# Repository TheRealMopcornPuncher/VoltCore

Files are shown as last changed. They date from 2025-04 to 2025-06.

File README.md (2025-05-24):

# VoltCore

A battery-powered variation of the common Cartesian 3d printer. Design specifications are subject to change.

Build volume: 100x100x65mm
Profile: Small
Battery: 24v 6ah lifepo4

VoltCore is a portable solution for 3D printing that allows an operator to print for one hour on a battery. This design attempts to solve the problem of environments devoid of immediate power via outlets or chargers connected to infrastructure.

- Amaya Allison & Jonathan Gallo

Image of printer

# Bill of Materials - VoltCore

| Item # | Description | Vendor | Part Number | Qty | Cost ($) | Purchase Link |
|---:|:---|:---|:---|---:|:---|:---|
| 1 | 2020 Aluminum Extrusions (200mm) | Amazon - VICHSAMWY | nan | 2 | $14.99 | https://www.amazon.com/European-Standard-Anodized-Aluminum-Extrusion/dp/B09JSNM85H/147-5007961-6940856 |
| 2 | Ender 3 Mainboard | Amazon - Creality Store | nan | 1 | $39.99 | https://www.amazon.com/Creality-Motherboard-Upgraded-Printer-TMC2225/dp/B0C77RBBP5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 |
| 4 | 24V 6Ah Lifepo4 Battery | Amazon - KBT | nan | 1 | $44.99 | https://www.amazon.com/letoom-LiFePO4-Rechargeable-Phosphate-Batteries/dp/B0DSRT3BB8 |
| 3 | E3D V6 Hot End Full Kit | Amazon - Ovenot | nan | 1 | $13.50 | https://www.amazon.com/Wangdd22-1-75mm-Printer-Extruder-Accessories/dp/B06XBXDJY3 |
| 4 | 1/8 inch PET Expandable Braided Sleeving | Amazon - Alex tech store | nan | 1 | $7.99 | https://www.amazon.com/25ft-Expandable-Braided-Sleeving-Sleeve/dp/B071G5L29C |
| 5 | T Nuts | Amazon - Socell | nan | 1 | $7.99 | https://www.amazon.com/Socell-180Pcs-Hammer-Fastener-Assortment/dp/B07Z4YH6NP |
| 6 | Belt Idler Pulley | Amazon - WINSINN | nan | 1 | $8.99 | https://www.amazon.com/WINSINN-Idler-Pulley-Timing-Aluminum/dp/B07BPHPYTN |
| 7 | Belt Timing Pulley | Amazon - Saipor | nan | 1 | $6.99 | https://www.amazon.com/Saiper-Aluminum-Synchronous-Compatible-Printer/dp/B07M9FT3H1 |
| 8 | Screws, Nuts, and Washers (Assortment/Kit) | Amazon - wugongshan | nan | 1 | $13.98 | https://www.amazon.com/Assortment-Machine-Washers-Phillips-Slotted/dp/B0BN297MP5 |
| 9 | Linear Rail (200mm) | Amazon - NUIBBYED | nan | 1 | $16.99 | https://www.amazon.com/MGN12H-Linear-Carriage-Printer-Machines/dp/B0BYVCXK88 |
| 10 | Voltage Regulator | Amazon - WWZMDiB | nan | 1 | $9.99 | https://www.pcbway.com/ |
| 11 | Flexible Shaft Coupler | Amazon - Eewolf | nan | 1 | $9.99 | https://www.amazon.com/Coupler-Flexible-Couplings-Printer-Eewolf/dp/B07BBP4H8C |
| 12 | Voron M4 Extruder Parts Kit | Amazon - FTVOGUE | nan | 1 | $15.60 | https://www.amazon.com/FTVOGUE-Accessories-Extrusion-Mechanism-Hardware/dp/B0BFCCTYDY |
| 13 | 5015 24v Blower Fan | Amazon - Richer-R | nan | 1 | $6.77 | https://www.amazon.com/Richer-R-Printer-Turbofan-Accessories-rotation/dp/B07CLG7RQY |
| 14 | 4020 24v Axial Fan | Aliexpress - YTF Technology | nan | 1 | $1.30 | https://www.aliexpress.us/item/3256803185681643.html |
| 15 | CR-Touch Leveling Probe | Amazon - Skouphy | nan | 1 | $39.00 | https://www.amazon.com/Creality-Leveling-Compatible-Mainboard-Printer/dp/B098LQ9WPX |
| 16 | NEMA 17 Stepper Motors | Stepperonline | 17HS13-0404S1 | 4 | $8.48 | https://www.omc-stepperonline.com/nema-17-bipolar-1-8deg-26ncm-36-8oz-in-0-4a-12v-42x42x34mm-4-wires-17hs13-0404s1 |
| 17 | Linear Ball Bearings | Amazon - Edoneery | nan | 1 | $11.99 | https://www.amazon.com/LM8UU-Linear-Bearings-Length-Printer/dp/B087WPGQ8T/147-5007961-6940856 |
| 18 | Linear Rods (200mm) | Amazon - akkacm | nan | 1 | $15.99 | https://www.amazon.com/Hardened-Chrome-Plated-Linear-Printer/dp/B09YRLS34X |
| 19 | (ONLY ONE OF EACH) 200mm Lead Screw and Lead Screw Nut | Amazon - VICHSAMWY | nan | 1 | $4.99 | https://www.amazon.com/400mm%EF%BC%8815-75-Inches%EF%BC%89Tr8x8-Thread-Printer-Machine/dp/B0BWYL5RNC |
| 20 | Split Shaft Collar | Amazon - PATIKIL | nan | 1 | $7.29 | https://www.amazon.com/PATIKIL-Thickness-Aluminum-Locking-Industry/dp/B0DDC83NVB |
| 21 | Needle Roller Thrust Bearings (2x) and Washers (2x) | Amazon - uxcell | nan | 1 | $6.19 | https://www.amazon.com/uxcell-Bearings-Diameter-Thickness-Hardness/dp/B07PDXYQTJ |
| 22 | GT2 Belt 6mm | Aliexpress - 	3DPrinterSuper Store | nan | 1 | $3.79 | https://www.aliexpress.us/item/3256808197552885.html |
| 23 | PEI Magnetic Buildplate (120mmx120mmm) | Amazon - G-hubble | nan | 1 | $10.99 | https://www.amazon.com/120x120mm-Textured-Magnetic-Adhesive-Printer/dp/B09TXM7VFC |
| 24 | Bowden Tubing | Amazon - Creality Store | nan | 1 | $5.99 | https://www.amazon.com/dp/B09WDGNZQM |
| 25 | Raspberry pi 0w | Amazon - Raspberry pi | nan | 1 | $22.78 | https://www.amazon.com/Raspberry-Pi-Zero-Wireless-model/dp/B06XFZC3BX |

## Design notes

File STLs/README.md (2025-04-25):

The following files are in this directory and are required for the final build:

TL;DR - Print 1 of every file except "ModF_Angle_Bracket.stl" (x10), "ModB_Belt_Clamp_Y" (2x), and "ModF_Plastic_Risers.stl" (4x)

/bed:
---
ModB_Bed_Mount.stl x 1
ModB_Belt_Clamp_Y x 2
ModB_Rail_Spacer.stl x 1
ModB_Underplate.stl x 1
---

/extruder
---
ModE_Extruder_Mounting_Bracket.stl x 1
---

/frame
---
ModF_Angle_Bracket_5.2mm.stl x 12 (alternative available)
Or
ModF_Angle_Bracket.stl x 12
ModF_Left_Linear_Tensioning_Bracket_A.stl x 1
ModF_Left_Linear_Tensioning_Bracket_B.stl x 1
ModF_Mainboard_Mounting_Bracket.stl x 1
ModF_Plastic_Spacer.stl x 4
ModF_Right_Linear_Tensioning_Bracket_A.stl x 1
ModF_Right_Linear_Tensioning_Bracket_B.stl x 1
ModF_Spool_Holder_Riser.stl x 1
ModF_Spool_Holder_Tube.stl x 1
ModF_Y_Axis_Stepper_Mount.stl x 1
ModF_Z_Axis_Stepper_Mount.stl x 1
---

/gantry
---
ModG_Left_Tensioning_Bracket_A.stl x 1
ModG_Left_Tensioning_Bracket_B.stl x 1
ModG_Right_Tensioning_Bracket_A.stl x 1
ModG_Right_Tensioning_Bracket_B.stl x 1
ModG_Sliding_Idler.stl x 1
ModG_Stepper_Spacer_&_Mounting_Plate.stl x 1
---

/printhead
---
ModP_Belt_Clamp_X x 1
ModP_CR_Touch_Mount.stl x 1
ModP_Hotend_Clamp_A.stl x 1
ModP_Hotend_Clamp_B.stl x 1
ModP_Printhead_Mounting_Bracket_A.stl x 1
ModP_Printhead_Mounting_Bracket_B.stl x 1
ModP_Radial_Cooling_Fan_Mount.stl x 1
---

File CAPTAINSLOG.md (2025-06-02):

Made by: @Amaya and @Jonathan G 
Repository link: https://github.com/TheRealMopcornPuncher/VoltCore
BOM: https://docs.google.com/spreadsheets/d/1q4xtd6th8_cM6Qn8iwp2R4_8qS0gYeFDji75B9E_PQI/edit?usp=sharing
Images: https://docs.google.com/document/d/1O2JPVw-2Jhm0MzPRCLd0zcRRRKDtKQYV07AwvWWCOpY/edit?usp=sharing

Fusion 360 PCB link: https://a360.co/4jejSvC (DEPRECATED - DOES NOT WORK)
Fusion 360 Printer assembly link: https://a360.co/3RkSeRq

Total hours so far: ~127 hours
- [x] I have a 3d printer or will be getting one before March 21st

---
NOTICE! Print files and quantity specifications listed in STLs folder on github repo. I'm printing all of the files in PLA with standard infill (lol) and 2mm layer height. Basic settings. Tolerances are baked into the models. 

This project has been resumed for the Highway event at Hackclub, per authorization of Dari aka Alex Ren

END OF NOTICE!

---
< Briefing >
A silly concept accidentally turned reality
Pitch: An extra portable and partially remote solution to printing without an active power source

---

# Day 0 - Preparations and planning

### Feb 4, 2025

I began by generating a timeline for me to operate within, as to avoid me procrastinating and not finishing the project at all.

**Deadline: Feb 11**

- Finalize battery system and power management.
    
- Generate a rough BOM (electronics, motors, extruder, frame materials, etc.).
    
- Confirm which parts I can salvage from my spare Sovol SV01 Pro.
    
- Research and select a control board + firmware (e.g., Klipper or Marlin).

**Deadline: March 31** _(Finalized Design & Parts Ordered)_

- Design a compact frame in CAD, ensuring it satisfies a small size profile (X and Y dimensions are 6-7 inches).
    
- Simulate motion system (belt routing, pulley positioning, etc.).
    
- Plan the mounting locations for electronics and battery.
    
- **Finalize the design and order all necessary parts.**

**Deadline: April 14** _(All Parts Arrived & Assembly Begins)_

- Assemble frame and install motors, belts, and pulleys.
    
- Wire up control board and power system.
    
- Perform first motion tests (homing, jogging, etc.).
    
- Mount and test the extruder and hotend (ensure >220°C capability).
    
- **All parts should be in by this date to stay on track.**

**Deadline: April 28**

- Flash firmware and configure motion system.
    
- Tune motion system and stepper settings.
    
- Ensure power consumption is within acceptable limits.
    
- Run first test prints and refine print quality.

**Deadline: May 4** _(Final Benchy Print Verified & Ready to Ship)_

- Complete final tuning and ensure prints are high quality.
    
- Verify folding mechanism and portability.
    
- Confirm battery efficiency for intended use.
    
- **Must have a successful Benchy print by this date!**

**Deadline: May 6** _(Ship Everything or Carry it with You)_

- Pack the printer securely for shipping.
    
- Ensure documentation and necessary tools are included.
    
- Consider taking it as a carry-on for guaranteed arrival.

Besides this, I've also done some research on suitable parts. Mostly minimal. Total time elapsed: 2 hours

# Day 1

### Feb 5, 2025

I felt pretty energized with the project today so I decided to start working on pushing my project into the tank with the others. (Started writing and journaling today, previous entry was made up for yesterday.) I intend to jot some stuff down into the BOM and continue fleshing out my solution for power. Mostly stuff from my first deadline/checkpoint.

I started my BOM by snatching and customizing a template for it off the web in google sheets. After creating the BOM, I started looking for the components I'd need to assemble the frame, and I got a recommendation for some of the nicest prices and highest class extrusions I could find from a company called 80/20 LLC.

After getting the link to the extrusion, I was going to start modeling it in Fusion 360, when I proceeded to fall down a rabbit hole of logo design. In the end, I installed Inkscape and began learning how to craft a nice looking logo to slap over the rest of this project.

I decided to take a break from learning how to use Inkscape. After hopping into a call with my brother and ranting about the project, he suggested I use a single motor for the Z-axis linked via a belt to support all sides of the bed (Maybe via linear rods/rails?)

Total time elapsed: 1 hr 40 mins

---

# Day 2

### Feb 6, 2025

Today was a little hectic so I'm mostly just pushing myself to keep going for the sake of progress. Maybe I'll get some coffee... besides the point though.

Attempts to fill out my bill of materials went pretty good today. I got a lot done in terms of meeting my Feb 11th deadline. The help of my brother, who's an experienced engineer, came in handy quite often since he knew more about this than I did, and told me whenever I added something that wouldn't work to the BOM, as well as giving me recommendations on where to look and what I could use.

I also am deciding to keep track of what 3d printed parts I'll need to model and make for this printer to function:

- Bed mounting bracket
    
- Extruder fan shroud and mounting bracket

Total time elapsed: 2 hrs 25 mins

---

# HIATUS PERIOD: Feb 6th - Feb 12th

### Project resumed.

I'll admit, I gave up. I didn't think I knew enough, I ran out of motivation, and there it just felt like this whole thing was a waste of time for someone inexperienced like me.

Then, I rejected that philosophy. Of course there was going to be hurdles, there always is. I just needed to get back up and keep working. Nothing I've ever done happened unless I told myself I could be capable, and I'm doing that right now.

---

# Day 3

### Feb 12th, 2025

Running partially behind schedule, I knew I needed to catch up, so I decided to use my time on this day to finish my B.O.M. and move on.

My biggest issue was the cost of the parts. In their current state, I was up to over 300 dollars, and not even completely done with the list. To cut down on cost, I began looking for cheaper alternatives to my existing parts.

I devised a plan regarding the frame: The bed would be 3d printed at a size contained inside of a 100mm by 100mm space and would be covered with masking tape. Frame will be joined with aluminum extrusions and metal brackets, then reinforced with 3d printed corner braces.

I ended up revising literally everything in my BOM and got the price down quite a bit. The next steps would be to figure out what I'm doing for my extruder and hotend, cooling fans, and my z axis.

Total time elapsed: 2 hrs

---

# Day 4

### Feb 17th, 2025

I ended up getting sick for a few days which kinda... super sucked, but I'm back and feeling moderately okay. I'm running low on time to meet my deadlines so it's time for me to reorganize and plan out what I'm doing next. Only really one of these needs a change.

**Deadline: Feb 20**

- Finalize battery system and power management.
    
- Generate a rough BOM (electronics, motors, extruder, frame materials, etc.).
    
- Confirm which parts I can salvage from my spare Sovol SV01 Pro.
    
- Research and select a control board + firmware (e.g., Klipper or Marlin).

I ended up finishing an entire disassembly in about an hour and a half.

Total time elapsed: 2 hrs

---

# Day 5

## March 30th, 2025

Panic time!!! The deadline is very very close and I don't entirely know if we'll be getting an extension. To combat this, I've invited one of my closest friends to help me with the project. It also helps that he knows significantly more than I do, and is an extremely fast worker. 

We've gotten the BOM pretty much completed, all that's left to do know is model and joint everything in Fusion 360 so we can see what we're missing and revise the BOM based on that data. Jonathan, my friend, ended up modeling a few things last night, which is why I'll be taking up modeling as much as possible for my current task of the day. 

I almost forgot to mention one of the more important changes we made to the project. We ended up having to change the motion system from corexy to cartesian. Ultimately, the decision was just made due to time constraints and the complexity of the corexy motion system, which we are simply not prepared for.

I intend to work all day.

Organization is key to this project, so I'm going to be modularizing and listing the parts of the printer I will need to model here:

Frame
	3x 100mm extrusions for the bottom
	2x 200mm extrusions for sides extending up
	1x 100mm extrusion for connecting 200mm extrusions at the top of the structure
	2x 200mm extrusions for the x-axis and the y-axis
Gantry (X-axis)
	Printhead: Extrusion and hotend assembly
	Stepper controlling movement
	200mm 2020 Extrusion
Buildplate/Bed
	Mounting solution to base of device
	200mm 2020 Extrusion
	(Mount higher in the structure to accommodate large battery)
Base
	Housing for electronics and IO/other interfaces
	3x 100mm 2020 Extrusions
Z-Axis or as I like to call it, "Elevator"
	Dual support from Z-axis lead screws, must allow gantry to travel up and down
	Stepper controlling movement
	2x 200mm 2020 Extrusions

Total time elapsed: 7 hrs

---

# Day 6

## March 31st, 2025

I made an immense amount of progress yesterday and I honestly feel like completing this project is very much possible. Although I had tasked my partner with creating a voltage regulator, I very stupidly forgot to specify what for... so I now need to create a voltage regulator. again. This time with the LM2576-5.0 voltage regulator, since *it* will work between the battery and the mainboard. Which, might I add, isn't much of an impressive battery TT

Since I'm very... uh... for lack of a better term uneducated, I'll be using Fusion 360 to design my PCB. Additionally, Fusion 360 and I seem to share that trait, so I'll need to give it some of the libraries myself, instead of being able to just find what I need in the software. Very fun stuff.

UPDATE: I let my partner know about the correct specifications and he agreed to revise it himself, yippie :D

I've also worked out our extruder situation considering the E3D V6 Hotend I picked earlier. This was important, because my stupid #$% didn't realize you... didn't have to design an extruder from scratch.... oh well.

We'll be using the Sherpa Mini.

All of this in mind... I'm fairly confident I can just- START with the final CAD model tomorrow :DD 
EXCITINGGGG

*I love you spring break <3*

Total time elapsed: 3 hrs

___

# Day 7

### April 1st

My computer exploded and I lost all of my project files.

Just kidding. :3

Today I've decided to model the full printhead. To do this, I'll need to create a holding mechanism or structure for the E3D V6 hotend that links up to the Sherpa Mini extruder. Shouldn't be too hard, but then, what do I know lol.

NOTES: Self supplying 2x motors with pre-fastened timing pulleys for the X and Y axis, self supplying 2x additional motors and flex couplings for Z axis (Will need to purchase lead screws). This leaves only one motor to be actually purchased for the extruder.

It's going to be tricky with clearance, but I just need to design an adapter between the E3D's obnoxious 16mm notch connector thingy and the even more obnoxious space consuming Voron M4 extruder (Which by the way we're using now instead of the Sherpa because it's so insanely inexpensive.)

Total time elapsed: 1 hour

---

# Day 8

### April 3rd

It's been an abysmal pain trying to use all of the models I've collected for this project for reasons beyond me. Despite that, I've continued to make progress, although extremely slowly. I've got no idea what I'm doing with this project and it's driving me insane.

Today, I hope to actually model the stupid gantry, but luck seems to despise me as of recent.

To make things different from my multiple prior attempts to design this, I'll be designing it in reverse, starting from the mount attached to the 2020 extrusion acting as a frame for the x-axis, and working my way up to the hotend.

Holy molay I forgot just how much music helps me to get out of depressive moods lol. I LOVE YOU RWBY SOUNDTRACK.

Also sidenote why do I write like... idk something fancy whenever I'm upset lol???

MODELING IS GOING GREAT I'VE DONE SO MUCH ON THE MOUNTING PLATE FOR THE PRINTHEAD YIPPIEEEEEE!!!

Update: Spent 3 hours modeling something I didn't need :D I LOVE LIFE GUYS I LOVE MY LIFEEEEEE!!!11111

(Also personal note: Pester my elder engineers more)

I know what I'm doing now. Just added a full kit of the ender 3's POM wheels and spacers to the BOM, so I'll just need to model or scrape those from somewhere to get them in Fusion 360 :P

GODSPEED TO YOU FUTURE ME

Total time elapsed: 4 hrs

---

# Day 9

### April 4th

New day, new stuff. I'm fetching the models for the "Isolation Column" and 5mm eccentric spacers I need to the POM mounted motion systems

Updating most of the spacers/washers, lock nuts, and other components in my final printhead/gantry assembly to fit with an M5 screw since I previously modelled them to interface with M4 screws.

After about 2 hours I finished redesigning the mounting plate for the printhead. Later today after a break, I'll model the notches for the ends of the belt and the mounting system for the extruder.

I forgot to log most of what I was doing so I'll speed run explaining all of it really really quickly. OKAY SO. I imported the aluminum extrusion (2020 x 200mm) and modeled everything around it, since HEY y'know, kinda a STUPID amount easier when you're modeling stuff in decending order of importance.

So anyways, I started with the extrusion, slopped in the POM Wheels and jointed them to the rail in Fusion 360, gave it a sliding joint because why the flip not (I spent way too much time doing that in school to not use it here), then I made a plate using the projected positions of the wheels hugging the extrusion. This was helpful because it allowed me to get a really good estimation of where the holes in the plate would need to be.

Then I had to research how to fasten the wheels to the plate and tighten them on the aluminum extrusion. To do this I simply stared at an image of the ender 3 and drank an abnormal amount of coffee before getting extremely jittery and crying over stupid stuff for like 2 hours. After this mindbogglingly stupid way of research, I learned what I was doing wrong. Eccentric nuts need a slot in the mounting plate to rotate in, otherwise they're useless.

Oh also yes I literally just stole I mean stole I mean stole I mean- borrowed the x-axis/gantry design of an ender 3. I LEARNED SOMETHING REGARDLESS, SO I DON'T WANNA HEAR IT, SHUSH.

BUT ANYWAYS, after figuring out what spacers to use, how the eccentric nut worked, where I could buy everything, etc. I got to work again. I put those holes into the mounting plate and then jointed everything together, spacers and all. That made me really happy and I thought I was done, but then I was like "wait no there's literally nothing on that plate", and so you'll never guess what I decided to do next. Actually I slept for like 10 hours, but AFTER THAT, I modeled.. heh.. you guessed it, a TRIANGLE SHAPED HOLE! ....It helped remove unnecessary material okay?

After wasting wayyyy too much time on that, I moved on to modeling the slots/notches for the belt, that was simple enough (HAHA NO JK IT TOOK HOURS AND AT LEAST 5 SEPERATE REDESIGNS. ALSO I CRIED AGAIN). After the notches were modelled I decided to move onto making a mount for the extruder, which took the most time by a LONG SHOT. I kept projecting sketches, revolving circular depressions, and otherwise just fumbling around with it until it looked semi-functionable. Then I fumbled with it some more and got this kind of like, pressure mount? You have to screw a plate that compresses the E3D V6 hotend into a groove that keeps it tightly secured. HOPEFULLY, THAT'S ENOUGH.

I already KNOW this is gonna be a major p.i.t.a. when I print it, but that's a future me problem.

Something ended up happening so I decided to work the rest of the night until early morning to take my mind off things, as I typically do to take my mind off of things.

Ended up modeling a shroud and mount for the 5010 blower fan I've decided to use for print cooling, so that's nice. It only took an additional 2 hours... TT

Christ I'm still going and it's 12:31 A.M.... waiiit I need to switch logs.

Total time elapsed: 12 hrs

---

# Day 10

### April 5th

Got my partner to start working on the project again, surprisingly we're both nocturnal. 

I did a lot today, not as much as yesterday, pretty sure that was like a one time thing (I ended up sleeping until after 12pm today, so safe to say we won't be trying that again lol).

Today I've decided to work on the Z-Axis and adding in the stepper motor for the x-axis, which should in all honesty be connected to the same mounting plate as the z-axis carriage. If you don't know what that means, I didn't either when my brother was explaining it, but after brute forcing the design a few hours, I think I understand it now.

Spent most of the day modeling the Z-axis when I learned I had to redesign almost everything because it couldn't be 3d printed and still function well.

yay.

Total time elapsed: 6 hrs

---

# Day 11

### April 6

I have today and maybe 1 or 2 hours (thanks American education system for taking away any liberty over my own personal life) to finish this entire design.

I do not believe it's enough time, considering I have to redesign literally everything to be under budget again, but I'm not going to sleep, so I intend to use every hour available.

Just a note, I have m3, m4, and m5 t-nuts

Current total cost of BOM excluding taxes and shipping sits at $239.86

Spent a little time organizing everything into folders in fusion 360 so I can stop scrolling all the damn time.

NOTE: Use M4 screws to mount printhead carriage. 

Added 0.5 tolerance to the hotend mounting brackets.

Printhead assembly now contains both interference fittings for the linear bearings (2 rods per axis, excluding Y with it's linear rail), and a mounting bracket for the hotend. I'll add the print cooling fan and BL-Touch later today.

Finished the printhead at the end of the day
Fasteners are obnoxiously large.

Total time elapsed: 8 hrs

---

# Day 12

### April 8th

Hoping to finish designing the gantry today. I created a tensioning bracket to hold the linear rods yesterday, a simple clamping shape that fits around the rods and is held together via one M4 and two M3 screws. Didn't document it though because I only just finished designing that.

My current design challenge of the day is modifying that same bracket to include space for a linear bearing (For the Z axis) and a stepper motor to drive the X axis.

I am currently approaching this design by adding the linear bearing on the back of the tensioning bracket. Adding the lead screw will be harder, though. After asking my brother (Thank you big brooooo lmfaooo) I learned that the hardware I need is called a "lead screw nut", and I'll need to model a part on the tensioning bracket to hold it very, very securely. I found a pack on amazon, 250mm lead screws and lead screw nuts, perfect for the project. I added them to the BOM, and got to work adding the lead screws into my CAD model for the gantry. It'll be a little bit difficult since I'm trying to keep the size of the tensioning bracket down as much as possible, however it should be possible to fit them both onto the bracket if I move the linear bearing towards the center, and the lead screw somewhere near the edge.

Ended up opting for the kit with only one screw and one nut, so total cost is down to $244.95, which is dangerously close to my limit, but we're still floating.

I realized far too late that the tensioning bracket's current design makes it impossible for the x-axis to move, and that the way I had intended to move it originally wasn't possible to begin with. I'm now redesigning a small part on the tensioning bracket to make space for the new motion system, then I'll redesign a small part of the printhead to interface with the belt properly.

It took many hours, but after making things bigger and smaller over and over again, everything finally fits, and the parts are beautiful. I just have to design the right side version of the tensioning bracket for the linear rods and we're pretty much done for today! Gantry done and over.

Worked until really late, but the entire gantry is finally finished. Tomorrow, I'll work on the Z-axis.

Total time elapsed: 8 hrs

---

# Day 13

### April 9th

After about two hours, I fixed a few glaring issues with the gantry. I forgot to add an idler pulley to the right brackets (timing pulley was on the left side already), so I did that, and then I modified the print head so that the notches for the belt were in the correct locations and not on an entirely different axis... TT

Moving on- I'll be working on the z axis today. I don't actually know what that part is called- sorry.

I'm going to start by putting two linear rods in. That'll be the last two I have available from the BOM, so for the last axis (Y), I'll use my linear rail. To start, I need to collect the distance of the linear bearings (specifically their center), and replicate that with the position of the linear rods in the z axis part of the gantry... wait omfg this means I'm not done with the gantry doesn't it. Oh well.

When does this count as the frame in my books? Idk. I guess when you make A FRAME. ??? lol
From now on, I'm just going to call this next part "UPPIES" because I can't think of a technical term, and I'm chill like that

After a quick edit, I just changed the spacing of the linear bearing's centers to EXACTLY 220mm. I would have preferred 240, since the spacing would be like 20mm + 20mm (since 2020 extrusions) + 200mm (The extrusion between two extrusions), but I can get creative and make it work anyways.

Wait no technically this would count as part of the frame, because I'll need to design some of it for this anyways-

WELL, FRAME TIME.

Wait also I just realized- 220mm spacing works perfectly because I forgot to divide the 20mm length since we're imagining the center of the aluminum extrusion... Yay :3

After moving stuff around in CAD for a bit, I settled on a layout/setup for the frame. It was so perfect, that I didn't even need 300mm long 2020 extrusions, only 200mm long ones, so I deleted the 300s from my BOM and saved a few bucks by just doubling the 200s. Very nice :D

I created a specialized corner bracket to hold the linear rods in place using the same kind of tensioning plate as the x-axis portion of the gantry.

It looks really really ugly though lmfao.

To drive the Z axis I've decided to take a page out of the Prusa Mini's book and mount the stepper at the top of the printer, facing down.

Is current total $244.6 with the additional hardware. Cut costs ever so slightly by ditching the limit switch and finding a cheaper 4020 axial fan.

Did a lot of research today and learned about thrust bearings, which is the additional hardware I mentioned earlier. It's extremely helpful for mounting the stepper upside down, but it's also nice that I learned something pretty cool today :D

Didn't get a whole lot done because of the research breaks, but I still did a lot today and I can be proud of that. I estimate I should finish this project either before or during Saturday. Before I end today's work, though, I'm going to add the new models for the new additions to the BOM. Just two things, won't take very long if I'm lucky enough to find premade step files for the parts.

Total time elapsed: 7 hrs

---

# Day 14
### April 10th

We're practically in overtime now and I need to finish everything immediately. I still have to fix a few things on the Z-axis, mount the electronics, finish the Y-axis, and find out our power situation. Let's begin then:

I DO not want to solve the battery issue, so I'll start with it. I need a battery that's close to 24 volts.

I have little to no experience, so I'm going to spend a few hours reading up on voltage regulators and creating PCBs in Fusion 360.

[ PROJECT TERMINATED AND RESUMED ON APRIL 14th ]

Total time elapsed: N/A

---

# Day 15
### April 14th

We're on a tight deadline as usual so I have to make this quick. This is the outlook of our current schedule by order of importance:

1. Revise BOM to operate within budget and time constraints (Today/Immediately)
2. Finish designing Z axis (Today/Immediately)
3. Finish designing Y axis (Tomorrow)
4. Extruder mounting and filament holder at top of frame (Tomorrow)
5. Electronics mounting and battery situation (Tomorrow)
6. Printer review (Tomorrow)
7. Purchase parts (After review, est. 4/15-4/17)
8. Assemble printer (When parts arrive, est. 4/22-4/23)
9. Test for any major issues and fix immediately (est. 4/22-4/23)
10. Ship battery to location (est. 4/23-4/24)
11. REP RAP!!! (May 16)

So, as the schedule suggests, I'll start by revising the BOM. We'll remove most things and rearrange them, starting with the battery. It's important that I get an estimate of the total cost of everything ASAP so my partner can find a suitable battery while we work in tandem.

The battery will be hot swappable now to ensure ease of installation when we ship it to the festival.

Keeping track of everything that I delete from the BOM:
1. Original GT2 6mm belts from Creality (Scrapped them myself)
2. Ferrule connectors (Don't need them anymore for new battery design)

I saved additional funds by disassembling the Sovol Sv01 I've been hollowing out completely.

Now that the BOM is revised, I'm going to continue modeling the rest of the motion systems while my friend works on our power situation.

Total time elapsed: 3 hrs

---

# Day 16
### April 15th

Modeling day. I need to have the entire thing ready for review for tomorrow.

I modified the brackets so that the screws wouldn't collide with the aluminum extrusions, then rejointed everything in the frame. Next up is assembling the thrust bearing housing bracket.

I'm looking at the weight distribution of the flipped Z axis motion system, and we'll most likely need to put something underneath the thrust bearing housing bracket. I suggest something rubber-like with an adhesive backing, but we'll most likely just shove a folded shirt under it at the actual festival.

Minor adjustments to the thrust bearing housing bracket were made to allow the top washer to make exclusive contact with the shaft collar, since the previous design had little to no clearance between the 3d printed part and the shaft collar, which would have rendered the thrust bearings useless.

I noticed that the gantry would need to be updated to accommodate our belts so I completely revamped the right clamps. For all of these clamps, I've modeled two brackets that hug the linear rod, one bracket always slightly thinner so that if the two halves were to touch, they would not form a complete circle. This intentional bit of removed material gives an offset that a screw can utilize to tighten around the linear rods.

With the same concepts I learned designing the bracket the first time, I strived to recreate it with a belt tensioner. After the revamp, I reassembled the gantry (had a few issues with Fusion randomly not letting me save things :/ thanks guys) and went to bed for my pre-act test the following morning (YIPPIIEEEE (not)).

Total time elapsed: 4 hrs

---

# Day 17
### April 16th, 2025

As crazy as it is to think about, I'm actually almost entirely done with my work. That's just completely insane to think about considering how for most of this project, I felt like I'd always have half a dozen more things to do until the end of time, but no. We're really in the home stretch (fingers crossed I didn't just jinx it.)

Today I plan to finish the Y-axis, and it'll be the easiest of the three to be entirely honest. It's comprised of 3 components (not always just in my design): the underplate (what I'm calling the thingy underneath the buildplate), the mounting bracket (shaped like an X, screws to the part underneath which is the next item), and the spacing bracket. 

It took barely more than 2 hours and I finished modeling all of the components. I then jointed everything and double checked if I missed anything. I forgot the belt. Obviously you... you kinda need that. TT.

In the upcoming parts of this journal I'll attempt to add images, not really sure how to yet but I'll figure it out. I just want to explain how everything works.

Few more issues to work out before we're done here. I didn't think when I was modeling the notches in the mounting bracket of the build plate, so they're on the wrong axis TT.

I've moved the notches slightly to the side, the stepper motor will need to be mounted on it's slide in order for the belt to slot in properly. I've also added a lot of structural support for the new notches, since they're hanging now, but I'm still worried the tension could cause problems later on. We'll keep moving on for now.

I finished designing the tensioner and the Y axis is done, we are approaching the finish line.

Mounting the extruder and creating a filament holder were by far, the easiest part of this entire project lol.

It took awhile, but I decided to create separate mounting plates underneath the bed in the remaining space of the frame. These plates would be problematic normally, but I created plastic risers to account for their low-clearance with the ground.

After all of that, we're done.

Well, with the bulk of it at least. I still need to clean everything up, prepare a portfolio of all the screenshots I've been taking, and submit my work for review for the "Infill" challenge.

In order of what I need to do and what:

1. Add screws into brackets
2. Retrieve all printable files and put into a folder on my computer or github (not sure where exactly, just make publicly accessible.)
3. Put all major screenshots into a google doc and add notes for context
4. Submit printer design for review to purchase parts

Total time elapsed: 9 hrs

---

# Day 18
### April 20th 2025

Purchased the parts a few days ago, and now we're just waiting for all of them to come in. I started assembling what we had today, which was all of the parts for the frame, bed, and the electronic mountings (excluding the voltage regulator).

At some point, Josef Prusa must have blessed me or something, because I literally FOUND Haribo gummy bears near my backpack that fell from my closet.

Thank you Josef... I think???

Assembling was and will be much harder than I initially theorized. It took a total of 4 hours to square the 4 2020 extrusions at the base of the frame and insert the extrusion with the fully assembled bed. I think the bed was the easiest part to design and assemble out of the entire machine. A few redesigns were necessary to keep screw management in check (There was far to many M4s being used and we don't have that many), as well as some redesigns for design errors. I think that we'd be much more re-assured with a backup voltage regulator, so I'm going to do some research to find one that we can get for cheap in case our custom regulator dies/shorts. 

And for the millionth time, we have battery problems. The voltage regulator we ordered is most definitely not up to code, so we're gonna have to order a new one...

I've had to make a few redesigns as I'm assembling, mostly to the brackets, as well as adding some stuff in where there should've initially been supporting brackets.

Personal note:
Following parts need a redesign before continuing:
- ~~Y Axis Idler and Tensioning Bracket (Make thicker to use an M3)~~
- ~~Extruder mounting bracket (Change to M3)~~
- ~~Filament mounting bracket (Change to M4 x 20mm)~~

Total time elapsed: 7 hrs

---

# Day 19
### April 21

More parts arrived. I'll be assembling the Voron M4 extruder later today when the parts finish printing, until then, I have what I need to continue assembling the frame.

There's a lot of issues now, these linear bearings don't fit in any of the parts, and I used screws that we don't have in the cad model. SERIOUS redesign binge or this doesn't work, and that cannot happen.

Stuff that works so far:
- Angle brackets
- All bed parts
- Filament holder (with slight modifications)

Screws used so far (tracking M4 and M5):
- M4 x 10 (16)
- M5 x 10 (8)

Stuff to redesign/design:
- ~~Anything with linear bearings to diameter of 15.35 instead of 15.1~~
- Completely redesign right bracket for gantry (Using M3 x 20 not M3 x 30)
- Redesign both idlers (M3 x 30 does not exist)
- New voltage regulator bracket
- ~~Thrust bearing housing (Bearings are too low and not enough screw clearance)~~
- CR Touch mounting bracket (No cable clearance)
- ~~Y axis stepper mounting bracket (Overhang makes it JUST too fat to use)~~
- ~~Extruder mount (Backside is JUST too close to the frame)~~
- Printhead clamps (M3 x 40mm screw doesn't exist)

Stuff redesigned:
- ModF_YAxis_Idler_&_Tensioning_Bracket.stl
- Y axis stepper mounting bracket
- Thrust bearing housing
- Extruder mount

To make my life easier, I concluded that I'll redesign all the listed files, as well as the entire gantry.

Total time elapsed: 6 hrs

---
# Day 20
### April 22

The following modules are complete and do not require further adjustment until a test involving the entire printer is conducted:
- Frame (Generic structure, angle brackets only)
- Extruder

What I finished today: Complete mounting and assembly of the Mobius extruder. (Voron M4 extruder kit).

Total time elapsed: 5 hrs

---

# Day 21
### April 23

I've managed to disassemble the bed and am now going to take the time to redesign a clamping system for the belts so that they may be attached properly this time.

After redesigning the bed, I decided to use my time to work on the gantry, which I've been putting off for a few days. I wanted to make the design much more organized and much cleaner than the last time, since it was previously so messy that the file decided to straight up off itself mid-modeling session and destroyed a bunch of stuff. To do this, I'm employing the same design solutions I came up with for the gantry previously, only this time I'm designing them all together, instead of smaller and uncontrolled edits of a larger part. Sorta like resolving a puzzle that didn't change.

The gantry is in reality, a stepper motor with a lead screw nut and a supporting/alignment structure of your choice (in this case, linear rods). The left side of our gantry is a tensioning bracket for the linear rods, where the lead screw nut resides, and a mount for the X-axis stepper motor. The right side is the same thing, but with a (typically adjustable) idler instead of a stepper.

I finished redesigning the gantry after awhile, and honestly the revised version is much cleaner and a little bit more compact. I have no idea if it works, that's obviously the idea, but we won't know until the parts finish printing and I won't be awake when that happens.

Did a lot today, got the Y axis working (FINALLY.) and finished remodeling the gantry. Tomorrow, assuming the gantry assembles good, I'm going to move on to finishing up the Z axis modifications. It's still not working.

Total time elapsed: 6 hrs

---

# Day 22
### April 24

Not a lot done today, mostly just minor redesigns and whatnot. Added screw-tightened clamps to the bed since the previous method to hold them in place was just not working, fixed up the gantry some more (some stuff didn't fit), and that's about it. The bed works now, in theory, and the gantry is almost done being perfected.

Total time elapsed: 4 hrs

---

# Day 23
### April 25

Spent some time to redesign the printhead today, I'll be printing the revised parts momentarily, but I wanted to fix up the X axis idler body, since it didn't quite work out the first time. Tolerances are way too out of whack with the M4 nut we're using to tension the idler; it literally bumps into the idler pulley and prevents it from being screwed in place. Not ideal.

After redesigning the printhead and sending it off to the printer, there were a few more things I needed to do with the new files. First, and most importantly, I need to add it to the complete assembly in CAD, so we have a finished model of the revised printer. At this point, there is only one thing dysfunctional in our design, the Z axis thrust bearing housing bracket, and it may not even be necessary considering how well the printer seems to old it in place with absolutely no help.

The next thing to do is revise the entire github, there's been so many changes in the design that I may as well take the time to dump all the old files and replace them with one zip of all the printable parts.

Lastly, I'll have to make a few adjustments with some more images and files per the recommendation of Dari, the event organizer. 

Checklist of updated README.md in STLS folder of the github repo:

- [x] Printhead
- [x] Gantry
- [x] Extruder
- [x] Bed
- [x] Frame

After finishing the reorganization, I decided to continue with adding Dari's recommendations, before I collapse from sleep deprivation. Remember to not stay up until 2 AM regularly, kids!

Files have been added, we are good for now. I'll let you all know how it goes horribly wrong when I wake up from my nap and all the printed parts I left running explode or something else equally as absurd.

Aaaand about 3-4 hours later I woke up. Good news and bad news. Good news, most of the stuff I printed works. Bad news, I have a really annoying headache. Moving on.

The extruder clamp is a bit too fat, it's hard to slip on without interfering with the preinstalled fan duct. To solve this, I'll simply shrink it's profile vertically. Additionally, the tolerances for the linear bearings are ever so slightly too big. It's not sticking in the print. The holes to access the belt tensioner are too small for any screwdriver I have either. I did come up with a small idea while assembling the functional parts, though. Since the wires for the radial cooling fan are very short, it would be a good idea to use a cable chain. It might also look very cool, so that's a plus. 

I ended up sending another print with some revisions to fix the earlier mentioned issues. I'll see how that goes, but I wanted to address something else first. The bed. There's less than a millimeter of clearance with the belt clamps screwed in, so I'm going to make a new spacer that's a millimeter taller or two.

Total time elapsed: 5 hrs

---

# Day 24
### April 26

Good news! The Y axis is completely done and functions. I have to test the Z axis for any wobble once the printer is fully assembled, so far it's looking a little iffy. 

The printhead assembled pretty good, the wires are a little hard to manage, and I think we'll have to extend some of them (luckily I just so happen to have 16 guage wire literally LYING around in a box), but past that it looks pretty good. Before I close/screw the gantry shut, the printhead needs to be a completed module. In order to do this, I will need to fix the printhead mounting bracket (the one with the linear bearings), since it one, cannot hold the linear bearings, and two, has no belt clamping mechanism. I made at least 4 redesigns for the belt clamp, before finally stopping on one with a screwable plate like I used on the Y axis.

Hopefully it works when it's done printing.

Additionally, my friend/partner Jonathan is coming over to my place so we can share our work and continue fixing the machine in-person.

We finished assembling the X axis after an insane amount of fumbling and makeshift solutions (all of which were entirely my fault for cutting the belt slightly too short). The reprint of the printhead mounting bracket was also a success and now functions on the printer's gantry. Pretty much every module is functional (theoretically), except for the thrust bearing housing. Moving on, we'll get to work on the electronics.

While my partner works on getting a bracket modeled for the voltage regulator, I ended up finishing the cable chain I mentioned earlier. It's really funny to me how nearly everything I've designed has led to me creating the same design choices as other people when I realize why they did what they did. I.e. remove material here so that they can move, but leave some here so you don't need supports. Stuff like that.

Checklist:
- [ ] Extend wires to nominal length using 16awg wire
- [x] Put buck converter on the frame 
- [ ] Connect buck converter to mainboard
- [ ] Route wires through cable chain 
- [x] Connect to mainboard

Total time elapsed: 5 hrs

---

# Day 25
### April 29th

After meeting in person to test the voltage regulator with my partner, we determined that the regulator was in fact dysfunctional and we ended up having to return it to get a new one. After the replacement arrived we tested it again, and it worked with a 12v power source, whereas the previous one had failed completely. We didn't have enough time to hook it up to the battery, but I'm fairly confident that at this point, it's going to work as expected

Total time elapsed: 2 hrs

---

# Day 26
### May 3rd

Today, I decided to dedicate my time to shortening the wires we currently have (excluding the stepper motors) so that the cable management is significantly easier and the printer doesn't just have 2 meter cords hanging off of it in an impractical mess of hapharzardly thrown together garbage.

To do this, the following connections will be modified. I've also decided that we will only extend wires, not shorten them (as to avoid any major and irreversible mistakes.)

Cable guide:

1. Extruder Fan Wires
2.  Print Cooling Fan Wires

---

Once the cables are done being modified, I will slide them into an expandable cable braid and put that cable braid into a cable chain for additional support and rigidity that's capable of avoiding collisions with the printer's frame and components.

With this step done, I'll be ready to connect the mainboard to the power source (from the voltage regulator), which my partner should be working on in the meantime. Another calibration will be necessary since the new voltage regulator isn't calibrated to our current voltage (24V output), so we'll of course need to do that first and foremost. 

I expect that if we work diligently, we should be able to finish the project by the end of tomorrow. Though, if we cannot meet this weekend, we'll need to meet in person sometime during the school week, and that tends to be an annoying impedance to our workflow.

Second thought, there's still the software side of things. We created a printer configuration in advance to upload to the printer's mainboard when we were ready, but I think we'll need to make some adjustments to it before we're DONE done. Once klipper functions, we'll be ready for a real test.

I noticed some sagging along the gantry due to the plastic clamps of the linear rods starting to deform under pressure, so I decided to reprint/modify them to increase the strength of the tensioning brackets.

Total time elapsed: 2 hrs 

---

# Day 27

### April 9th

After setting up another meeting to finally get our voltage regulator operational, I met with my partner today to hook said regulator to the battery so we could test it.

After the regulator is calibrated, mounted to its final position, and wired to the mainboard, we should be ready to proceed with extending the wires like I intended in previous logs. With all of that done, the physical printer is ready for firmware, and finally a system-wide test.

If all goes according to plan, we should be ready for the "pre-flight" checklist several days ahead of schedule. Perfect for fixing mishaps and last minute screwups.

Here's to hoping we don't monumentally obliterate our work leading up to this point.

Total time elapsed: 1 hour

---

# Day 28
### April 14th

Absolute chaos, project is still not working, parts need to be reprinted, firmware does not work in the slightest capacity at all. I'm losing my mind, there's so much to do and it's school and life too not just this. Working as fast as hard as I can, just to get it all done. For the love of god please.

I'm going to reattempt to flash the firmware. Once I can get this working, I will do the basic calibration required to get it print-ready. After that we'll focus on cable management and rebuilding faulty parts with the filament holder.

I've tried virtually everything I possibly could to get the MCU to be detected by the pi but no matter what I do, it never seems to make a change. While I continue to troubleshoot the SD card, I've switched my pi to work on reprinting some more stuff for the filament holder issues (low clearance, snaps filament and spool unwinds causing catastrophic issues if actually printing)

Total time elapsed: 1 hrs

---

# Day 29

### April 24th

After getting permission from Alex, we're continuing this project and making it actually work! As well as severely upgrading our major oversights.

The following upgrades will be implemented:
- Extend height and modify frame
- Fix motherboard issues
- Create custom voltage regulators for both the raspberry pi and the motherboard, respectively
- More to come later on as we work

Total time elapsed: 1 hrs

---

# Day 30

### June 1st

Happy pride loves <3

Today, I'll be remodeling and rejointing the CAD assembly of Voltcore into a new and improved design that should actually work in real life this time.

To begin, I'll reassemble the frame.

Bottom frame image
(Bottom frame assembly)

Took me a minute to remember how the hell you put images here, but I'm doing it more often from now on for Alex's sake. (NOT MAD - I SHOULA DONE THIS FROM THE START, IK)

One of the major issues with the way we assembled the printer in CAD before stemmed from the fact that we were using a single file to combine minor modules into one single device. This creates major issues later down the road when you need to change things because suddenly, the ONE poorly modelled bracket you created 17 log entries ago has broken 87 other joints in the file. To fix this on "take two" of this project, we'll be finalizing the designs of major modules and combining them into the final printer only when said modules are completed in their own respective folders and files.

My current dilemma is picking whether or not I should fully assemble the major modules or do that in the complete printer CAD assembly file.

Or, I could make two versions of the major modules, split by assemblies with all their respective components or just the bare frame structures.

I think I'll just finish the assemblies with all their components.

Slightly more assembled bottom frame image
(With Y axis attached)

The bottom frame still needs the electronics mountings, but I think I wanna opt instead for a side mount this time around.

Speaking of the electronics, we need mounting for the following:
- Voltage regulator from battery to the mainboard
- Voltage regulator from mainboard OR battery into the RPI for Klipper firmware
- Mainboard

Jeez, with a side mounted mainboard and RPI we really are just ripping pages out of Prusa's book aren't we TT oh well.

Anyways, we'll leave the bed for now and work on the gantry.

In progress image of upper frame/gantry
(Extended 100mm in height from older versions)

We previously had issues with the filament spool holder not having enough clearance, and our solution to that in the past significantly increased the size profile of the printer, so I've remodeled the entire component to make use of vertical space.

Spool holder image
(Improved spool holder)

For the remaining components I need to add for this upper part of the frame, we need the extruder, and the side mounts for our electronics.

After that, we should be ready for a full assembly with the hardware (screws and whatnot) and all components put together :D

Though, the belt tensioner for the gantry needs a serious upgrade, so I may be forced to redesign the entire thing again.

Total time elapsed: 3 hrs

---

# Day 31

### June 2nd

Today will be dedicated to attempting to finalize the CAD assembly of all previous modules for Voltcore (since we are redoing everything). Afterwards, I will spend my time working on the new components.

To get started, I'll be working on 

Total time elapsed: 

---

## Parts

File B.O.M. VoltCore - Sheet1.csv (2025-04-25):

Bill Of Materials
Item # (Green = Purchased) | Description (Highlighted = owned already) | Vendor (Red = Change) | Part Number | Qty | Cost ($) | Link to Where to Purchase
1 | 2020 Aluminum Extrusions (200mm) | Amazon - VICHSAMWY | N/A | 2 | $14.99 | https://www.amazon.com/European-Standard-Anodized-Aluminum-Extrusion/dp/B09JSNM85H/147-5007961-6940856
2 | Ender 3 Mainboard | Amazon - Creality Store | N/A | 1 | $39.99 | https://www.amazon.com/Creality-Motherboard-Upgraded-Printer-TMC2225/dp/B0C77RBBP5
4 | 24V 6Ah Lifepo4 Battery | Amazon - KBT | N/A | 1 | $44.99 | https://www.amazon.com/letoom-LiFePO4-Rechargeable-Phosphate-Batteries/dp/B0DSRT3BB8
3 | E3D V6 Hot End Full Kit | Amazon - Ovenot | N/A | 1 | $13.50 | https://www.amazon.com/Wangdd22-1-75mm-Printer-Extruder-Accessories/dp/B06XBXDJY3
4 | 1/8 inch PET Expandable Braided Sleeving | Amazon - Alex tech store | N/A | 1 | $7.99 | https://www.amazon.com/25ft-Expandable-Braided-Sleeving-Sleeve/dp/B071G5L29C
5 | T Nuts | Amazon - Socell | N/A | 1 | $7.99 | https://www.amazon.com/Socell-180Pcs-Hammer-Fastener-Assortment/dp/B07Z4YH6NP
6 | Belt Idler Pulley | Amazon - WINSINN | N/A | 1 | $8.99 | https://www.amazon.com/WINSINN-Idler-Pulley-Timing-Aluminum/dp/B07BPHPYTN
7 | Belt Timing Pulley | Amazon - Saipor | N/A | 1 | $6.99 | https://www.amazon.com/Saiper-Aluminum-Synchronous-Compatible-Printer/dp/B07M9FT3H1
8 | Screws, Nuts, and Washers (Assortment/Kit) | Amazon - wugongshan | N/A | 1 | $13.98 | https://www.amazon.com/Assortment-Machine-Washers-Phillips-Slotted/dp/B0BN297MP5
9 | Linear Rail (200mm) | Amazon - NUIBBYED | N/A | 1 | $16.99 | https://www.amazon.com/MGN12H-Linear-Carriage-Printer-Machines/dp/B0BYVCXK88
10 | Voltage Regulator | Amazon - WWZMDiB | N/A | 1 | $9.99 | https://www.pcbway.com/
11 | Flexible Shaft Coupler | Amazon - Eewolf | N/A | 1 | $9.99 | https://www.amazon.com/Coupler-Flexible-Couplings-Printer-Eewolf/dp/B07BBP4H8C
12 | Voron M4 Extruder Parts Kit | Amazon - FTVOGUE | N/A | 1 | $15.60 | https://www.amazon.com/FTVOGUE-Accessories-Extrusion-Mechanism-Hardware/dp/B0BFCCTYDY
13 | 5015 24v Blower Fan | Amazon - Richer-R | N/A | 1 | $6.77 | https://www.amazon.com/Richer-R-Printer-Turbofan-Accessories-rotation/dp/B07CLG7RQY
14 | 4020 24v Axial Fan | Aliexpress - YTF Technology | N/A | 1 | $1.30 | https://www.aliexpress.us/item/3256803185681643.html
15 | CR-Touch Leveling Probe | Amazon - Skouphy | N/A | 1 | $39.00 | https://www.amazon.com/Creality-Leveling-Compatible-Mainboard-Printer/dp/B098LQ9WPX
16 | NEMA 17 Stepper Motors | Stepperonline | 17HS13-0404S1 | 4 | $8.48 | https://www.omc-stepperonline.com/nema-17-bipolar-1-8deg-26ncm-36-8oz-in-0-4a-12v-42x42x34mm-4-wires-17hs13-0404s1
17 | Linear Ball Bearings | Amazon - Edoneery | N/A | 1 | $11.99 | https://www.amazon.com/LM8UU-Linear-Bearings-Length-Printer/dp/B087WPGQ8T/147-5007961-6940856
18 | Linear Rods (200mm) | Amazon - akkacm | N/A | 1 | $15.99 | https://www.amazon.com/Hardened-Chrome-Plated-Linear-Printer/dp/B09YRLS34X
19 | (ONLY ONE OF EACH) 200mm Lead Screw and Lead Screw Nut | Amazon - VICHSAMWY | N/A | 1 | $4.99 | https://www.amazon.com/400mm%EF%BC%8815-75-Inches%EF%BC%89Tr8x8-Thread-Printer-Machine/dp/B0BWYL5RNC
20 | Split Shaft Collar | Amazon - PATIKIL | N/A | 1 | $7.29 | https://www.amazon.com/PATIKIL-Thickness-Aluminum-Locking-Industry/dp/B0DDC83NVB
21 | Needle Roller Thrust Bearings (2x) and Washers (2x) | Amazon - uxcell | N/A | 1 | $6.19 | https://www.amazon.com/uxcell-Bearings-Diameter-Thickness-Hardness/dp/B07PDXYQTJ
22 | GT2 Belt 6mm | Aliexpress - 3DPrinterSuper Store | N/A | 1 | $3.79 | https://www.aliexpress.us/item/3256808197552885.html
23 | PEI Magnetic Buildplate (120mmx120mmm) | Amazon - G-hubble | N/A | 1 | $10.99 | https://www.amazon.com/120x120mm-Textured-Magnetic-Adhesive-Printer/dp/B09TXM7VFC
24 | Bowden Tubing | Amazon - Creality Store | N/A | 1 | $5.99 | https://www.amazon.com/dp/B09WDGNZQM
25 | Raspberry pi 0w | Amazon - Raspberry pi | N/A | 1 | $22.78 | https://www.amazon.com/Raspberry-Pi-Zero-Wireless-model/dp/B06XFZC3BX

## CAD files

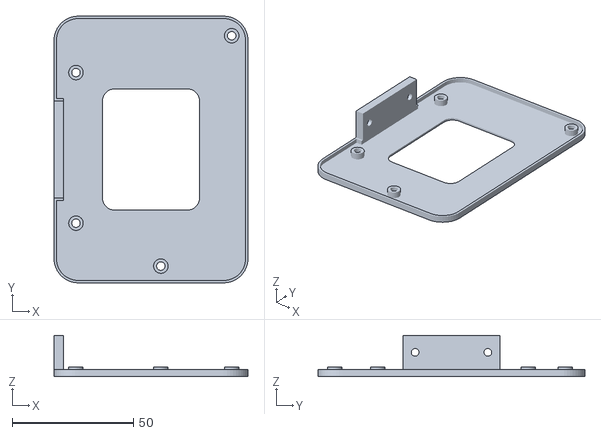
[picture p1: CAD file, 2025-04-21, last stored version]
STLs/frame/ModF_Mainboard_Mounting_Bracket.stl
80.0 x 110.0 x 17.0

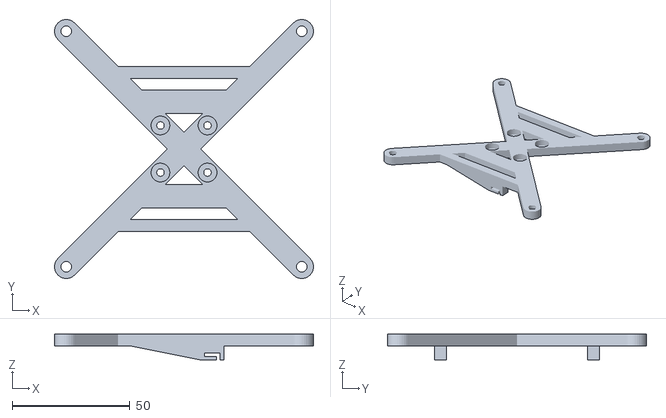
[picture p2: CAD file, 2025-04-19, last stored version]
STLs/bed/ModB_Bed_Mount.stl
110.0 x 110.0 x 11.0

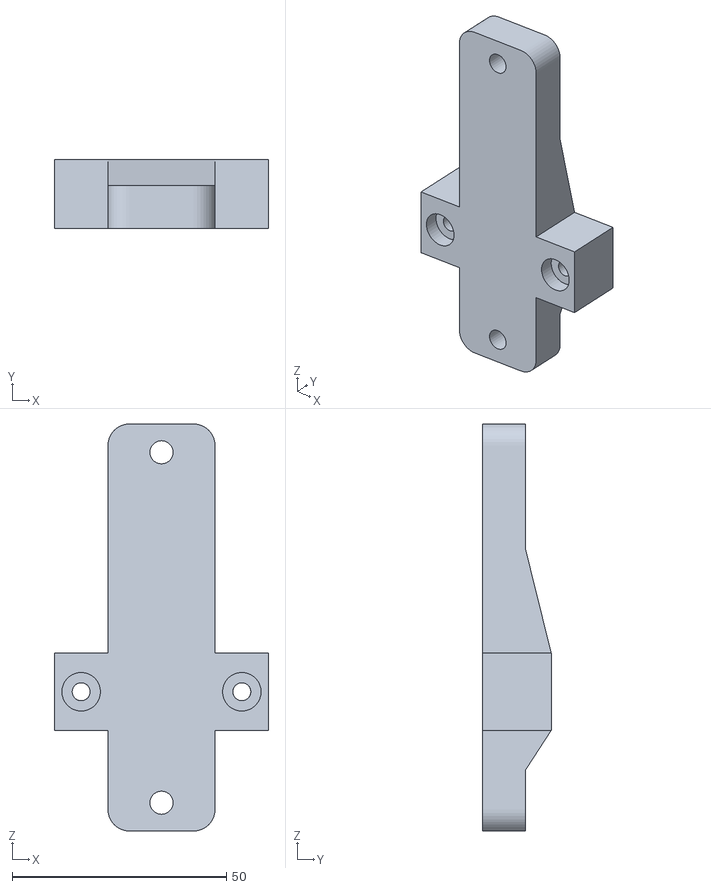
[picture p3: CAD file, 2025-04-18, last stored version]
STLs/extruder/ModE_Extruder_Mounting_Bracket.stl
50.0 x 16.0 x 95.0

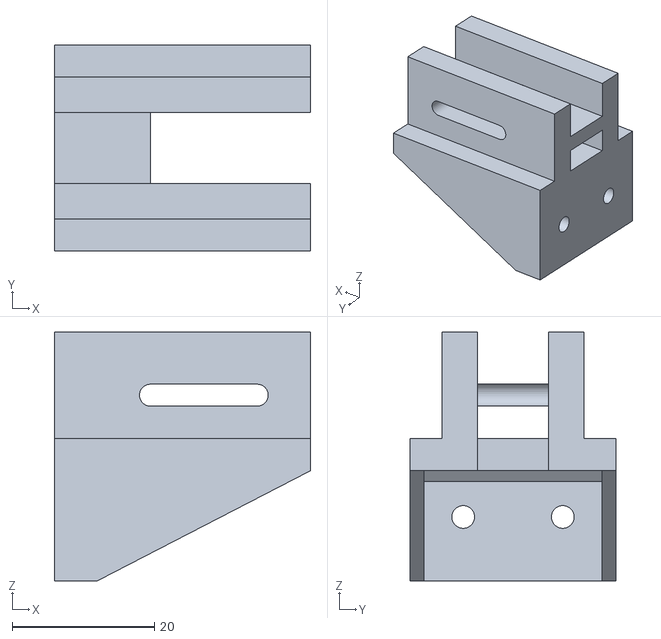
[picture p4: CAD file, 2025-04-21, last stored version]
STLs/frame/ModF_YAxis_Idler_&_Tensioning_Bracket.stl
36.0 x 29.0 x 35.0

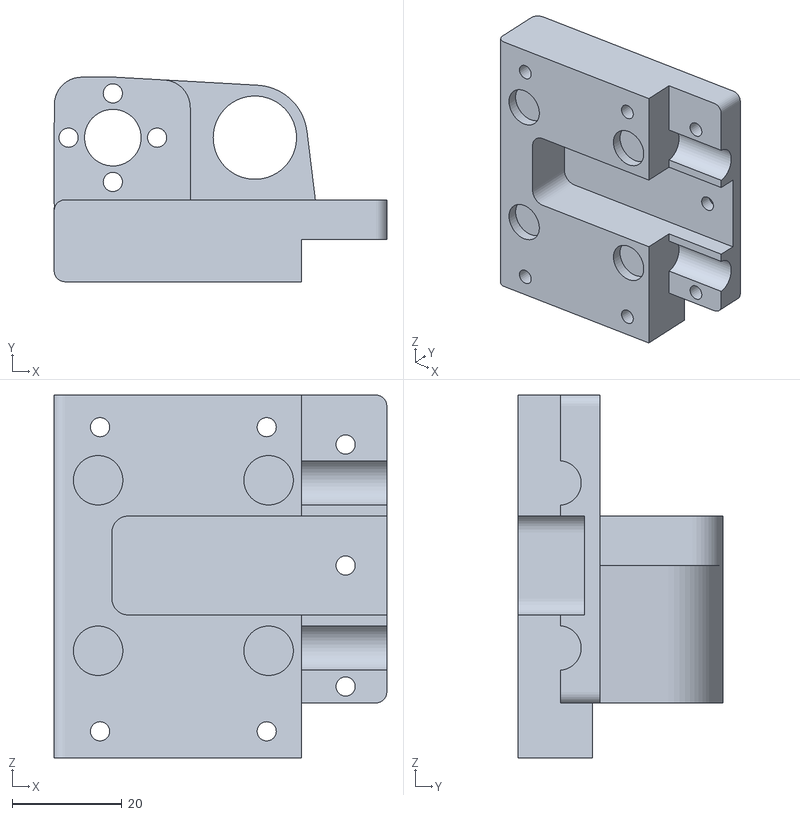
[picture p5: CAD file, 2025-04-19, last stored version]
STLs/gantry/ModG_Z_Bracket_Left_A.stl
60.5 x 37.2 x 66.0

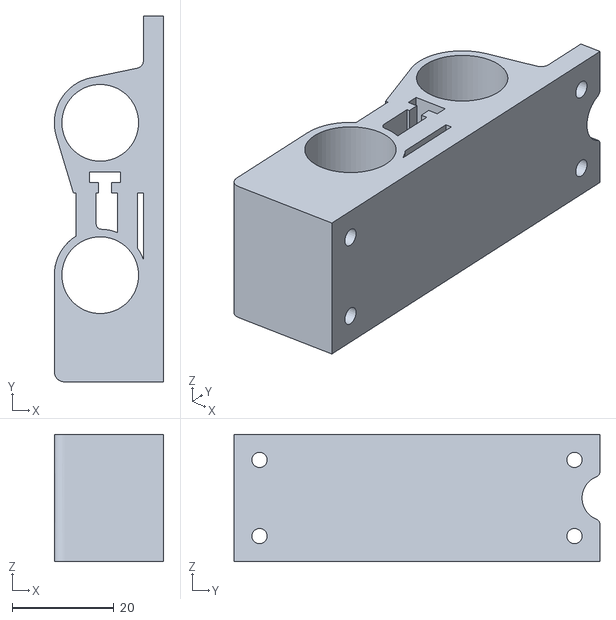
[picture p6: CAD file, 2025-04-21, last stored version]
STLs/printhead/ModP_Printhead_Mounting_Plate_B.stl
21.5 x 72.0 x 25.0

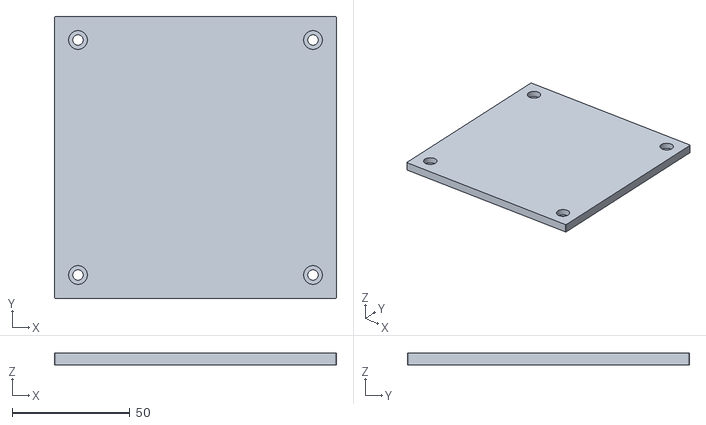
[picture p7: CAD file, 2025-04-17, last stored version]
STLs/bed/ModB_Underplate.stl
120.0 x 120.0 x 5.00

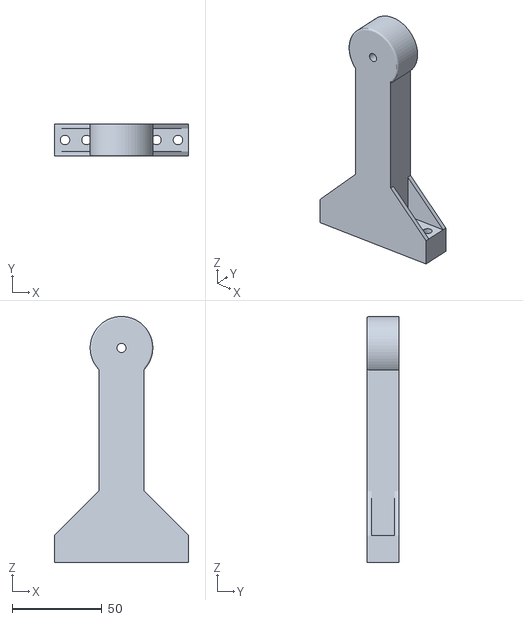
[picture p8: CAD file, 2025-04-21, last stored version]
STLs/frame/ModF_Spool_Holder_Riser.stl
75.0 x 18.0 x 137.2

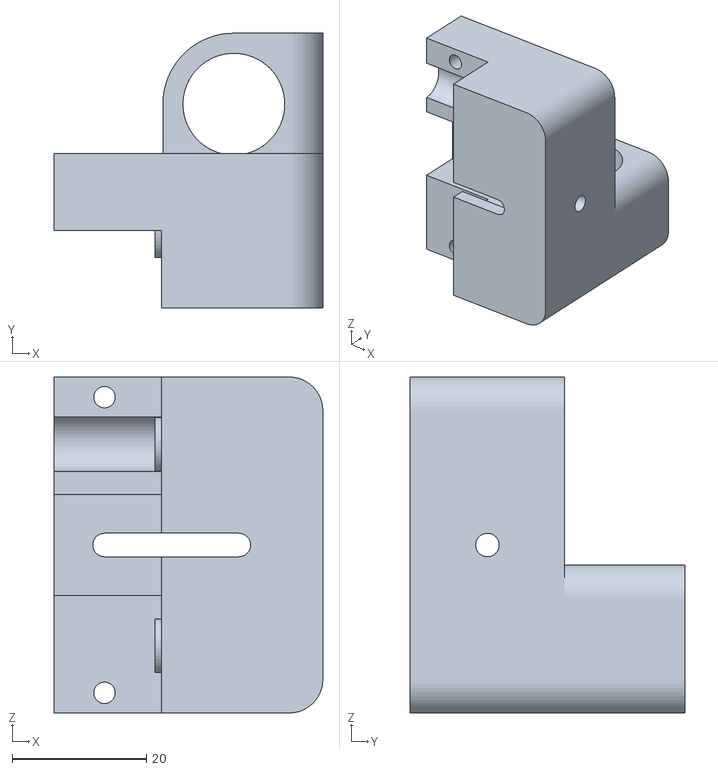
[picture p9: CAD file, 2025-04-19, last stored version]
STLs/gantry/ModG_Right_Belt_Tensioning_Block_A.stl
40.0 x 40.9 x 50.0

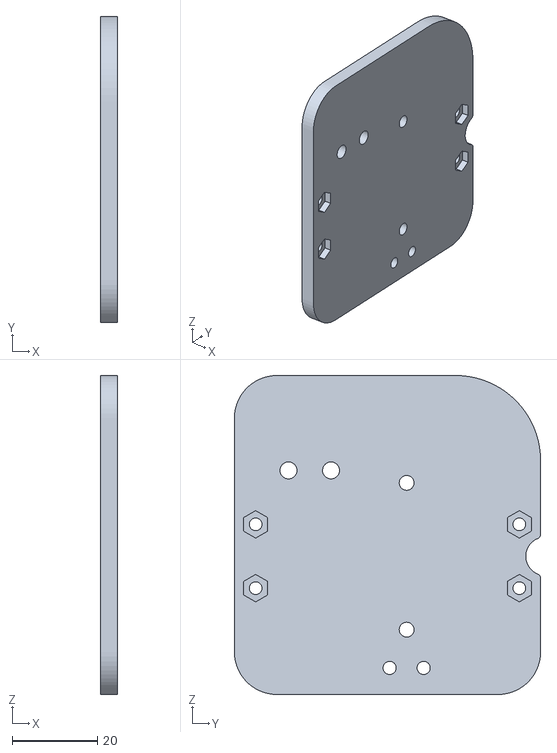
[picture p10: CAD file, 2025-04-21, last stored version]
STLs/printhead/ModP_Printhead_Mounting_Plate_A.stl
4.00 x 72.0 x 75.0

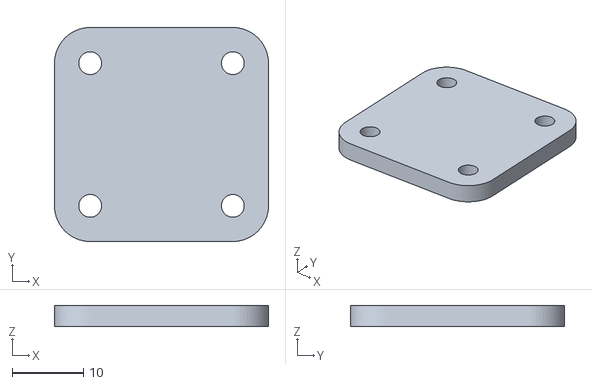
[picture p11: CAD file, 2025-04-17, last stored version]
STLs/bed/ModB_Rail_Spacer.stl
30.0 x 30.0 x 3.00

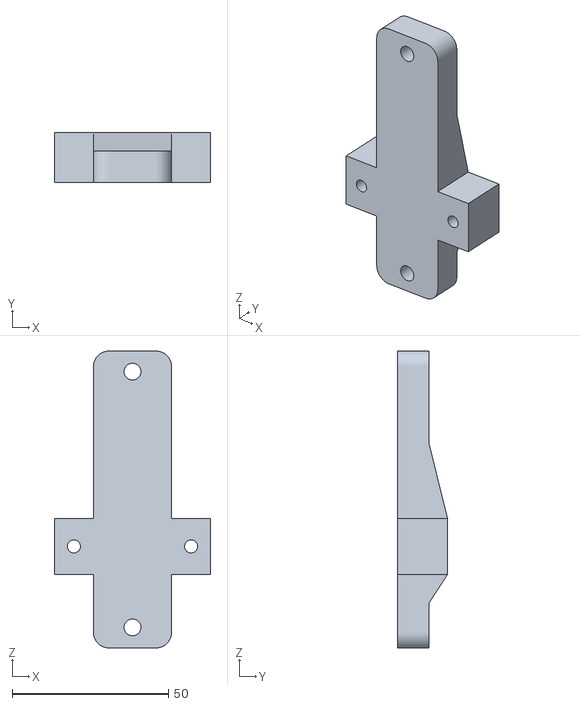
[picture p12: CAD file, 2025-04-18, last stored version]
STLs/extruder/ModE_Extruder_Mounting2_Bracket.stl
50.0 x 16.0 x 95.0

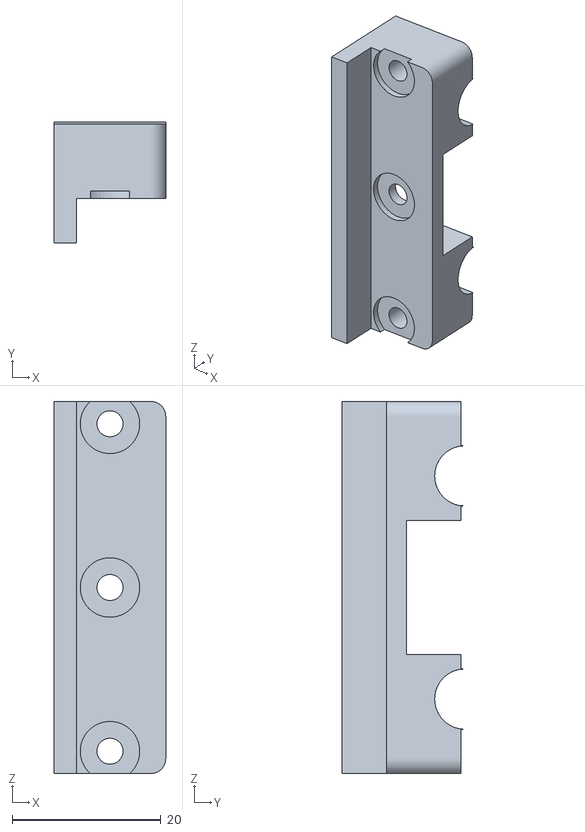
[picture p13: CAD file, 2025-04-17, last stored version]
STLs/gantry/ModG_Z_Bracket_Left_B.stl
15.0 x 16.2 x 50.0

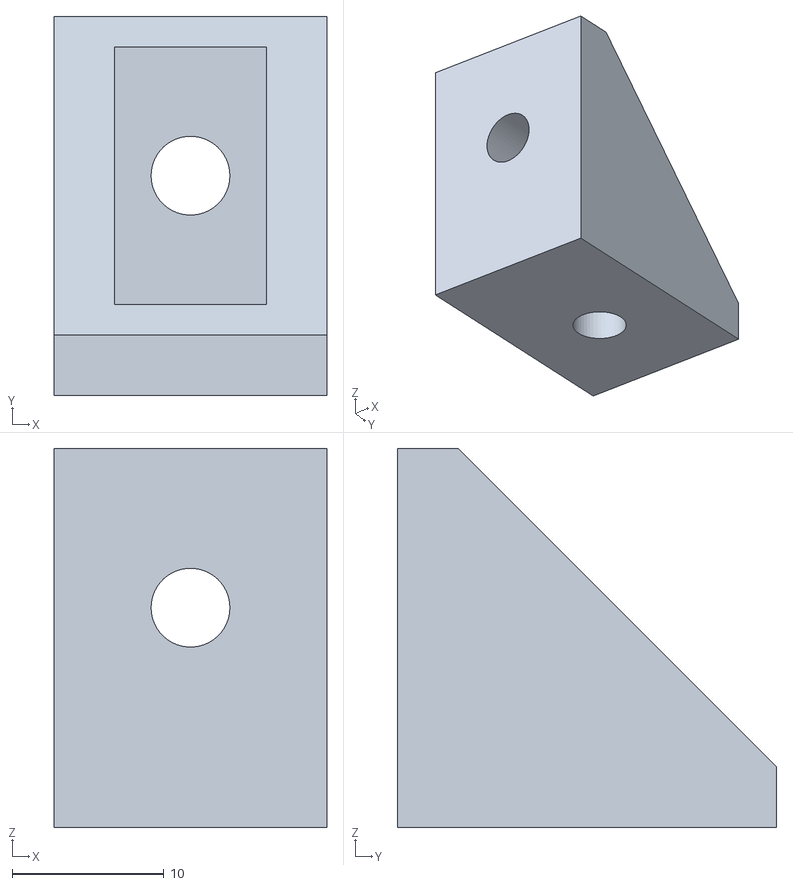
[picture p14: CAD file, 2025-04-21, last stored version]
STLs/frame/ModF_Angle_Bracket_5.2mm.stl
18.0 x 25.0 x 25.0

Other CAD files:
STLs/ModE_Extruder_Mounting_Bracket.stl
STLs/extruder/ModE_Extruder_Mounti2ng_Bracket.stl
STLs/gantry/ModG_Left_Bracket_Stepper_Spacer.stl
STLs/frame/ModF_Angle_Bracket.stl
STLs/frame/ModF_Angle_Bracket2.stl
STLs/frame/ModF_Left_Rod_Tensioner_A.stl
STLs/frame/ModF_Left_Rod_Tensioner_B.stl
STLs/frame/ModF_Plastic_Risers.stl
STLs/frame/ModF_Right_Rod_Tensioner_A.stl
STLs/frame/ModF_Right_Rod_Tensioner_B.stl
STLs/frame/ModF_Spool_Holder_Roll.stl
STLs/frame/ModF_Spool_Holder_Tube.stl
STLs/frame/ModF_Voltage_Regulator_Mounting_Bracket.stl
STLs/frame/ModF_YAxis_Stepper_Mounting_Bracket.stl
STLs/frame/ModF_ZAxis_Stepper_Mounting_Plate.stl
STLs/frame/ModF_ZAxis_Thrust_Bearing_Housing.stl
STLs/gantry/ModG_Hotend_Clamp_A.stl
STLs/gantry/ModG_Hotend_Clamp_B.stl
STLs/gantry/ModG_Right_Belt_Tensioning_Block_B.stl
STLs/gantry/ModG_XAxis_Belt_Tensioning_Pulley.stl
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
